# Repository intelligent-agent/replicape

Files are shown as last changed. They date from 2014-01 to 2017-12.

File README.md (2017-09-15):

    :::python
     _____           __
    | ___ \         | (_)
    | |_/ /___ _ __ | |_  ___ __ _ _ __   ___
    |    // _ \  _ \| | |/ __/ _  |  _ \ / _ \
    | |\ \  __/ |_) | | | (_| (_| | |_) |  __/
    \_| \_\___| .__/|_|_|\___\__,_| .__/ \___|
             | |                 | |
             |_|                 |_|

Replicape is a 3D printer cape for BeagleBone.  

### Features: ###

* 5 stepper motors (Trinamic TMC2100) (X, Y, Z, E, H)  
* 3 high power MOSFETs (PWM controlled) for 2 extruders and 1 HPB.  (12..24V)  
* 4 medium power MOSFETs (PWM controlled) for up to 4 fans/LED strips.  (12V)  
* 3 analog input ports for thermistors. noise-filtered inputs and option for shielding  
* 6 inputs for end stops (X, Y, Z).  
* 1 bus for Dallas 1W temperature sensor for monitoring the cold end. Up to 10 sensors can be added to the bus.  
* 2 servo outputs.  
* 1 inductive sensor input.  
* Programmable current limits on steppers motor drivers (SMD). No need to manually adjust a pot meter.  
* Microstepping individually programmable for each SMD from 1 to 256.  
* All steppers are controlled by the Programmable Realtime Unit (PRU) for hard real time operation.  
* Compatible with [Manga Screen](https://bitbucket.org/intelligentagent/manga-screen)  
* Single 12 to 24V PSU, fans are still 12V.  
* Compatible with BeagleBone and BeagleBone Black (probably also green and blue).  
* Open source hardware and software. (CC BY-SA)  
* Software written in Python for maintainability and hackability.  
  
This is the repository for the hardware, the "firmware" (Redeem) has a [separate repository](https://bitbucket.org/intelligentagent/redeem)

### What is in here? ###

* This repository contains the files needed to reproduce the PCB and continue development.
* The latest revision is B3

### I want one! How much is it, and where can I get it? ###

It's $99 and you can [buy it in the store](http://www.thing-printer.com/product/replicape)

### I want to build my own board. How do I do that? ###

* Download the BOM and order the parts from Digi-key
* Send the GERBER files to a PCB manufacturer
* Get a reflow oven
* Populate the board

### I want a different version of this, who do I talk to? ###

Talk to Elias <elias at iagent dot no> 

### I have a Replicape, how do I wire it? ###
Look at the wiki page: [http://wiki.thing-printer.com](http://wiki.thing-printer.com)

### I want to read about the latest development of this board. Where can I do that? ###
The thing-prnter blog is a good place: [http://www.thing-printer.com/blog/](http://www.thing-printer.com/blog/)

### Who has contributed to this project? ###

* Elias Bakken
* Dirk Eichel
* Stoneshop
* Bent Furevik

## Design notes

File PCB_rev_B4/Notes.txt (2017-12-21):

TODO: 
 + Add 41 pin connector, place it near the Ethernet cable. 
 - Keep the connectors that we have, change end stop wiring, so they are not tied to common ground. 
 - 4 x 12V fans!
 - RTD drop in replacement, Add jumper to Select voltage divider for RTD1000
 - Double check the final price.
 - Add a second thermistor for measuring chamber tmeperature, use T1 for that.
 - Perhaps use pin 1 and 2 for T1? 
 - Check price on EuroCircuits for 2 and 15 boards. 

Notes: 
 + Needs to either move the BBB, longer 41 pin cable or add a mounting plate. 
 - Choosing horizontal 41 pin connector to keep profile low. 
 - Pin 9/10 Not connected to anything. Is this right? 
 - Choosing 0.3 mm traces for Stepper X and E, due to 24V input. 
 - Do not use keyed horizontal headers.

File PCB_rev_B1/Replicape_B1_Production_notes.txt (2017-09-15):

Solder mask color: Black
Silkscreen color: White
PCB Layers: 4

Copper thickness: 35um

Top copper layer: Replicape_B1.cmp
Inner copper layer 1: Replicape_B1.ly2
Inner copper layer 2: Replicape_B1.l15
Bottom copper layer: Replicape_B1.sol

Outline: Replicape_B1.pls

Solder stop mask top layer: Replicape_B1.stc
Silk screen top layer: Replicape_B1.plc
Cream frame top: Replicape_B1.crc

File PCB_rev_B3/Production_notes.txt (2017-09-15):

Solder mask color: Black
Silkscreen color: White
PCB Layers: 4

Copper thickness: 35um

Top copper layer: Replicape_B3.cmp
Inner copper layer 1: Replicape_B3.ly2
Inner copper layer 2: Replicape_B3.l15
Bottom copper layer: Replicape_B3.sol

Outline: Replicape_B3.pls

Solder stop mask top layer: Replicape_B3.stc
Silk screen top layer: Replicape_B3.plc
Cream frame top: Replicape_B3.crc

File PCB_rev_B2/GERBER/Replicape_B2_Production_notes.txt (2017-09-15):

Solder mask color: Black
Silkscreen color: White
PCB Layers: 4

Copper thickness: 35um

Top copper layer: Replicape_B2.cmp
Inner copper layer 1: Replicape_B2.ly2
Inner copper layer 2: Replicape_B2.l15
Bottom copper layer: Replicape_B2.sol

Outline: Replicape_B2.pls

Solder stop mask top layer: Replicape_B2.stc
Silk screen top layer: Replicape_B2.plc
Cream frame top: Replicape_B2.crc

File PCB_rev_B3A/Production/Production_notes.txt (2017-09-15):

Solder mask color: Black
Silkscreen color: White
PCB Layers: 4

Copper thickness: 35um

Top copper layer: Replicape_B3A.cmp
Inner copper layer 1: Replicape_B3A.ly2
Inner copper layer 2: Replicape_B3A.l15
Bottom copper layer: Replicape_B3A.sol

Outline: Replicape_B3A.pls

Solder stop mask top layer: Replicape_B3A.stc
Silk screen top layer: Replicape_B3A.plc
Cream frame top: Replicape_B3A.crc

Statistics: 
===========
Length: 107.30 mm
Height: 69.55 mm
Number of SMD pads: 825
Number of Through holes: 167

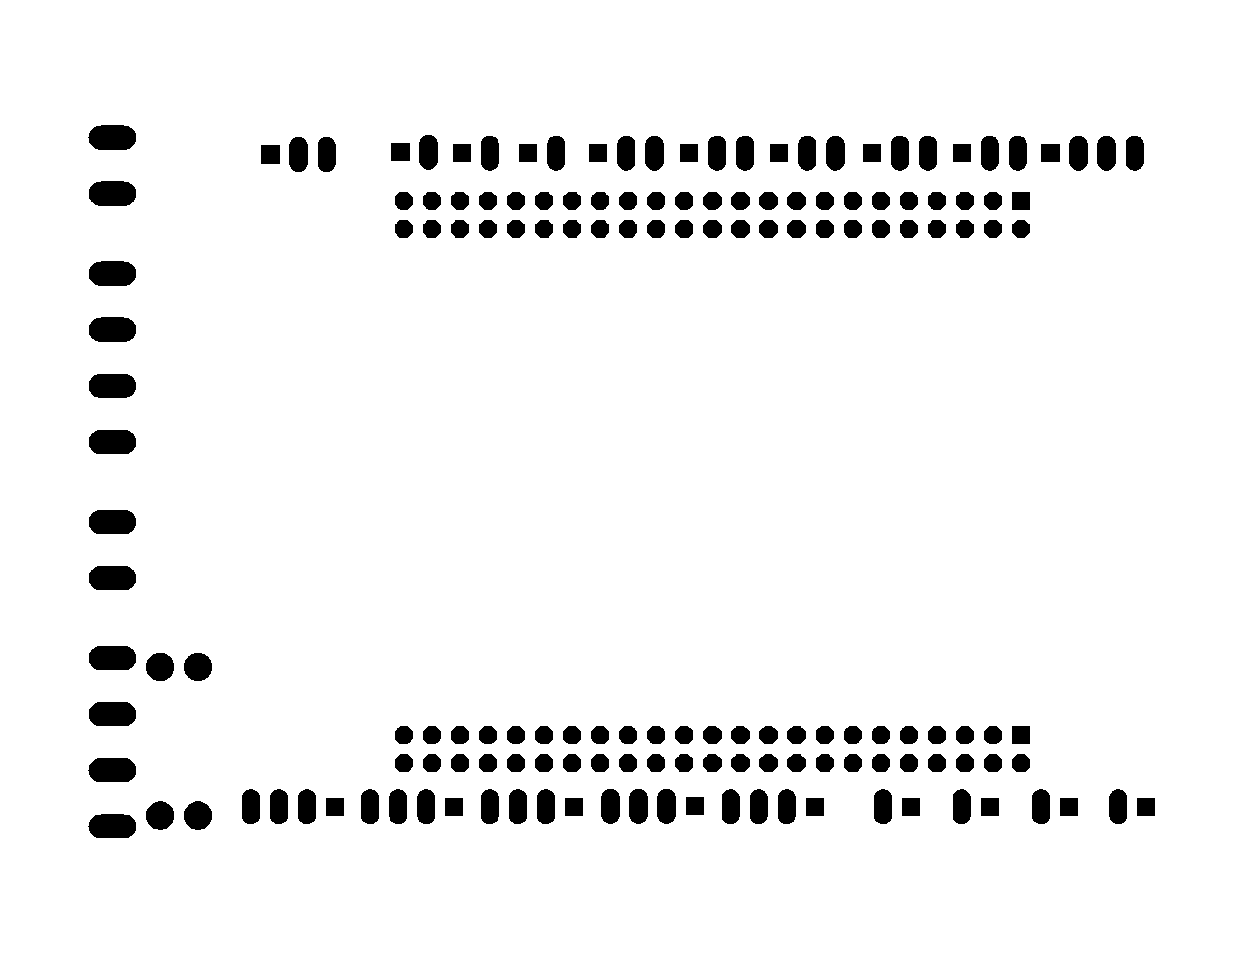
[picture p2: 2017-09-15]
PCB_rev_B2/eagleUp/eagleUp_Replicape_B2_bottom_mask.png

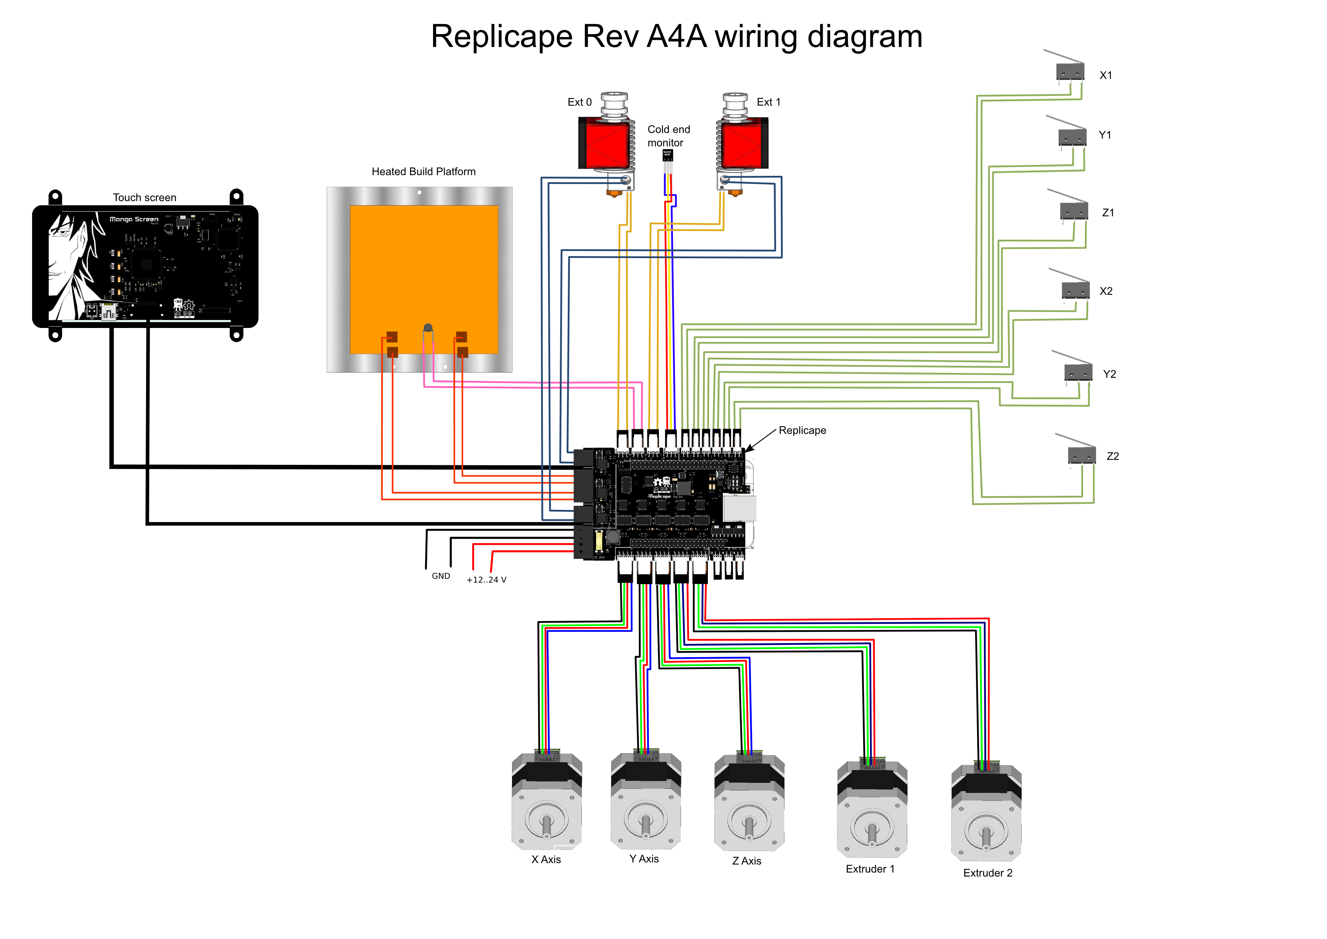
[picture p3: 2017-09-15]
PCB_rev_A4A/Replicape-wire-diagram.png

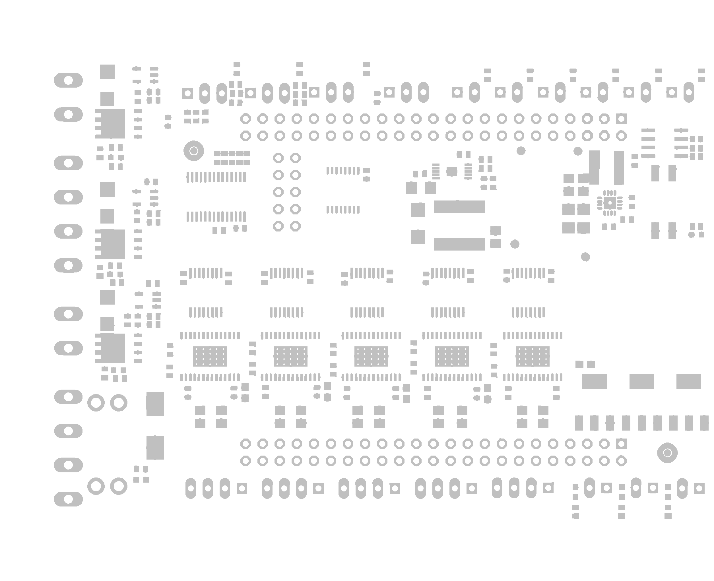
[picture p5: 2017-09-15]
PCB_rev_A4A/eagleUp/pads.png

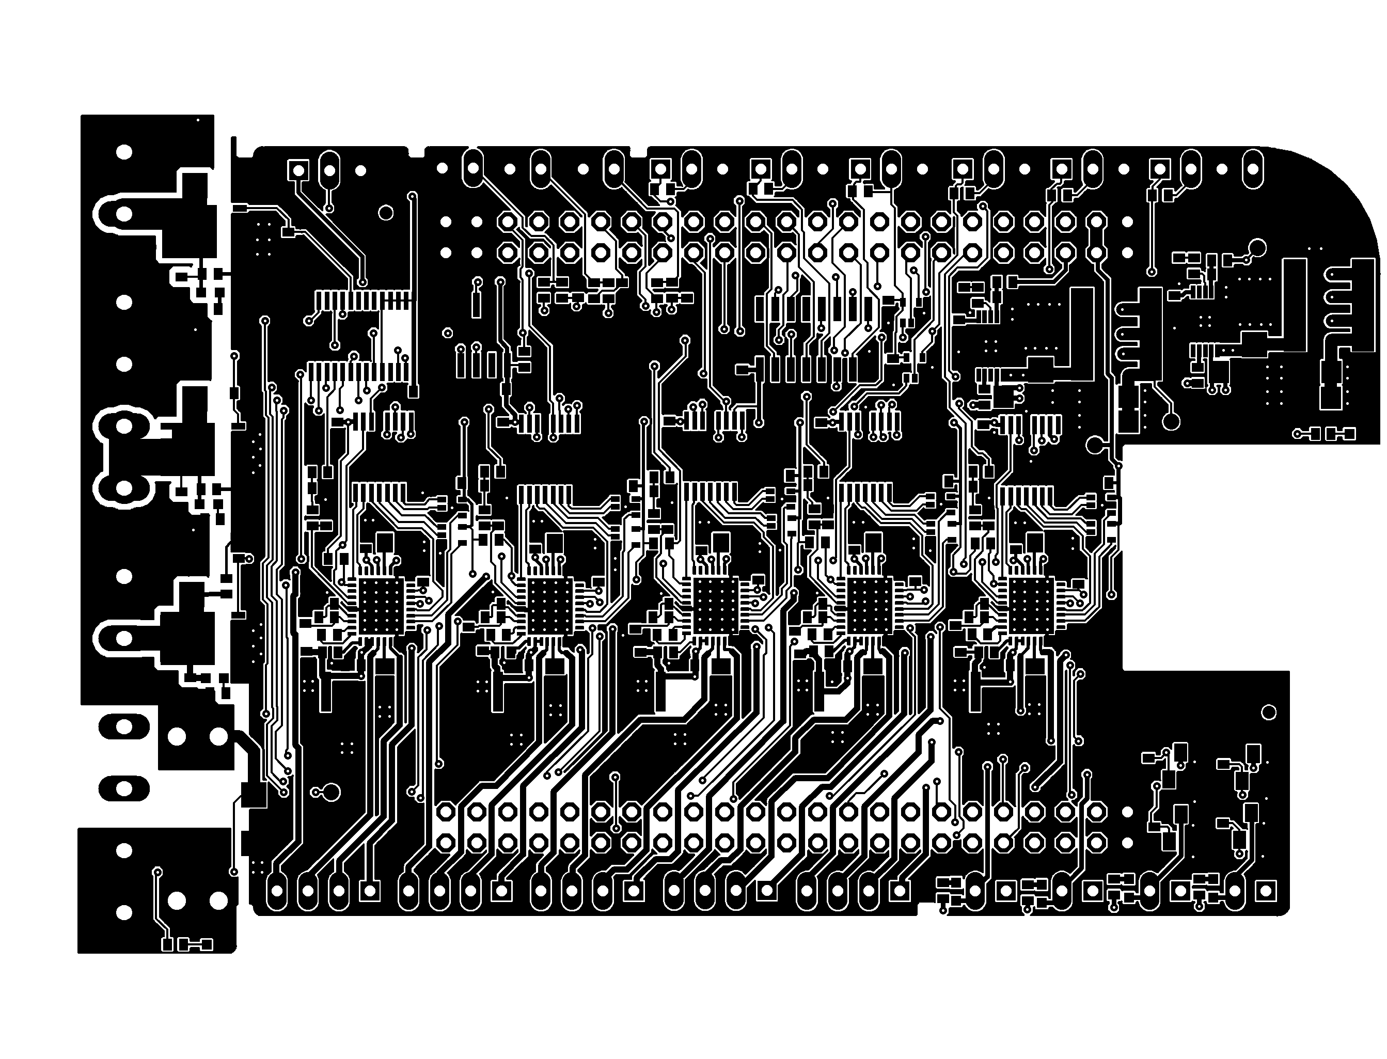
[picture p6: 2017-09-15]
PCB_rev_B2/eagleUp/eagleUp_Replicape_B2_top.png

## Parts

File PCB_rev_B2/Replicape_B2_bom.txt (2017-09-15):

Partlist exported from /home/elias/workspace/replicape/PCB_rev_B2/Replicape_B2.sch at 30.07.15 20:18

Qty Value                  Device                 Package              Parts                                                                                                                                                                                                                      Description                                                                       MF      MPN           OC_FARNELL OC_NEWARK PACKAGE  SUPPLIER          TOLERANCE TP_SIGNAL_NAME VALUE VOLTAGERATING
4                          NPN-TRANSISTOR_SOT23   SOT23                Q4, Q5, Q6, Q7                                                                                                                                                                                                             NPN TRANSISTOR                                                                                                                                                                                      
10  0.1R                   R-EU_R0805             R0805                R1, R2, R3, R4, R7, R8, R9, R10, R29, R30                                                                                                                                                                                  RESISTOR, European symbol                                                                                                                                                                           
45  0.1uF                  C-EUC0402              C0402                C2, C4, C5, C6, C8, C10, C13, C14, C15, C17, C19, C20, C22, C23, C27, C28, C29, C30, C31, C32, C35, C38, C40, C41, C42, C43, C44, C61, C63, C64, C66, C67, C69, C70, C71, C72, C73, C74, C82, C83, C84, C85, C86, C87, C88 CAPACITOR, European symbol                                                                                                                                                                          
5   100UF                  EEE-FK1V101XP-CASE-D8  CAPAE660X800N        C11, C16, C24, C34, C60                                                                                                                                                                                                    Aluminum Electrolytic Capacitors,Surface Mount Type                                       EEE-FK1V101XP 1850114    23T0869   CASE-D8  PANASONIC         ±20 %                    100UF 35V          
15  10K                    R-EU_R0402             R0402                R6, R22, R27, R31, R35, R37, R38, R39, R40, R41, R43, R49, R50, R58, R60                                                                                                                                                   RESISTOR, European symbol                                                                                                                                                                           
4   10nF                   C-EUC0402              C0402                C49, C50, C54, C55                                                                                                                                                                                                         CAPACITOR, European symbol                                                                                                                                                                          
6   10uF                   C-EUC1206              C1206                C47, C48, C52, C53, C80, C81                                                                                                                                                                                               CAPACITOR, European symbol                                                                                                                                                                          
1   120K                   R-EU_R0402             R0402                R42                                                                                                                                                                                                                        RESISTOR, European symbol                                                                                                                                                                           
2   1nF                    C-EUC0402              C0402                C51, C56                                                                                                                                                                                                                   CAPACITOR, European symbol                                                                                                                                                                          
5   2.2R                   R-EU_R0402             R0402                R52, R53, R59, R70, R71                                                                                                                                                                                                    RESISTOR, European symbol                                                                                                                                                                           
7   22-05-7028-02          22-05-7028-02          7395-02              X4, X5, X6, X7, X8, X9, X11                                                                                                                                                                                                CONNECTOR                                                                                               9731601    unknown                                                                          
6   22-05-7038-03          22-05-7038-03          7395-03              X1, X10, X13, X19, X22, X23                                                                                                                                                                                                CONNECTOR                                                                                               unknown    unknown                                                                          
6   22-05-7048-04          22-05-7048-04          7395-04              X12, X14, X15, X16, X17, X18                                                                                                                                                                                               CONNECTOR                                                                                               unknown    unknown                                                                          
5   22nF                   C-EUC0402              C0402                C1, C3, C7, C9, C39                                                                                                                                                                                                        CAPACITOR, European symbol                                                                                                                                                                          
2   33uH                   RT8040T330             NR8040T330           L1, L2                                                                                                                                                                                                                                                                                                                                                                                                                         
2   39K                    R-EU_R0402             R0402                R26, R44                                                                                                                                                                                                                   RESISTOR, European symbol                                                                                                                                                                           
31  4.7K                   R-EU_R0402             R0402                R5, R11, R14, R15, R16, R19, R20, R21, R23, R24, R25, R28, R32, R33, R34, R36, R45, R46, R47, R48, R51, R54, R55, R56, R57, R61, R62, R63, R64, R65, R66                                                                   RESISTOR, European symbol                                                                                                                                                                           
3   4.7nF                  C-EUC0402              C0402                C57, C58, C59                                                                                                                                                                                                              CAPACITOR, European symbol                                                                                                                                                                          
18  4.7uF                  C-EUC0402              C0402                C12, C18, C21, C25, C26, C33, C36, C37, C45, C46, C62, C65, C68, C75, C76, C77, C78, C79                                                                                                                                   CAPACITOR, European symbol                                                                                                                                                                          
1   44.3K                  R-EU_R0402             R0402                R12                                                                                                                                                                                                                        RESISTOR, European symbol                                                                                                                                                                           
3   4K7, 1%                R-EU_R0402             R0402                R13, R17, R18                                                                                                                                                                                                              RESISTOR, European symbol                                                                                                                                                                           
12  74AHC1G126DCK          74AHC1G126DCK          SC70-5               IC3, IC4, IC6, IC7, IC8, IC9, IC10, IC11, IC13, IC14, IC16, IC17                                                                                                                                                           Single Bus Buffer Gate With 3-State Outputs                                                                                                                                                         
3   AON6758                AON6758                8-DFN-EP-(5X6)       Q1, Q2, Q3                                                                                                                                                                                                                                                                                                                                                                                                                     
1   CAT24C256              CAT24C256              SOIC127P600X175-8N   U18                                                                                                                                                                                                                                                                                                                                                                                                                            
1   CC-BY-SA               CC-BY-SA               CC-BY-SA             U$3                                                                                                                                                                                                                                                                                                                                                                                                                            
1   CD4050BD               CD4050BD               SOIC127P600X175-16N  U19                                                                                                                                                                                                                        CMOS Hex Buffer/Converters                                                                CD4050BD      1740857    50R5062   16-SOIC  Texas Instruments                                             
2   F-2X23-                F-2X23-                DIL-100-2X23         P8, P9                                                                                                                                                                                                                                                                                                                                                                                                                         
2   FIDUCIAL1X2.5          FIDUCIAL1X2.5          FIDUCIAL-1X2.5       JP1, JP2                                                                                                                                                                                                                   Fiducial Alignment Points                                                                                                                                                                           
1   FUSE                   FUSE                   3557                 F1                                                                                                                                                                                                                         Fuse                                                                                                                                                                                                
6   MBRA340T3              MBRA340T3              SMA                  D1, D2, D3, D4, D5, D6                                                                                                                                                                                                     Surface Mount Schottky Power Rectifier                                                                                                                                                              
2   MSTBA2                 MSTBA2                 MSTBA2               X3, X21                                                                                                                                                                                                                    PHOENIX                                                                           FARNELL 1757242       3705171    71C4161                                                                          
2   MSTBA4                 MSTBA4                 MSTBA4               X2, X20                                                                                                                                                                                                                    PHOENIX                                                                           FARNELL 1757268       3705195    71C4163                                                                          
1   OSHW_LOGO_FILLX0200-NT OSHW_LOGO_FILLX0200-NT OSHW_FILLX200_NOTEXT LOGO1                                                                                                                                                                                                                                                                                                                                                                                                                          
1   PCA9685PW              PCA9685PW              SOP65P640X110-28N    U11                                                                                                                                                                                                                        16-channel, 12-bit PWM Fm+ I2C-bus LED controller                                         PCA9685PW     1854074    19T6398   TSSOP-28 NXP                                                           
2   RT8268                 RT8268                 MSOP10               U6, U10                                                                                                                                                                                                                                                                                                                                                                                                                        
5   SN74AHC595PW           SN74AHC595PW           SOP65P640X120-16N    U1, U2, U3, U4, U5                                                                                                                                                                                                         8 bit shift registers with 3-state  output registers                                      SN74AHC595PW  1741463    50R5930   TSSOP-16 Texas Instruments                                             
5   TMC2100-LA             TMC2100-LA             QFN36-PAD            IC1, IC2, IC5, IC12, IC15                                                                                                                                                                                                  Trinamic TMC2100 Stepper Motor Driver (5V...46V, 1.2A, peak 1.7A, 256 microsteps)                                                                                                                   
4   TPB1,27                TPB1,27                B1,27                3.3V, 5V, 12..24V, 12V                                                                                                                                                                                                     Test pad                                                                                                                                                                                            
9   blue                   LEDCHIP-LED0603        CHIP-LED0603         LED1, LED2, LED3, LED4, LED5, LED6, LED7, LED8, LED9                                                                                                                                                                       LED

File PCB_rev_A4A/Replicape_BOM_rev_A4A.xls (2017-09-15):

Digikey Part nr. | Desc | Ref | QTY 1 | P. ea 1 | P. ext 1 | QTY 500 | P. ea 500 | P. ext 500
Connectors
A19450-ND | CONN HEADER RTANG 2POS .100 TIN | X1, X4, X5, X6, X10, X11, X13, X19, X23 | 9 | 0.1 | 0.9 | 4500 | 0.03768 | 169.56
A19451-ND | CONN HEADER RTANG 3POS .100 TIN | X7, X8, X9, X12 | 4 | 0.14 | 0.56 | 2000 | 0.05733 | 114.66
A19452-ND | CONN HEADER RTANG 4POS .100 TIN | X14, X15, X16, X17, X18 | 5 | 0.18 | 0.9 | 2500 | 0.08734 | 218.35
WM7847-ND | CONN HEADER 4POS 5.08MM R/A TIN | X3, X21 | 2 | 1.04 | 2.08 | 1000 | 0.648 | 648
WM7953-ND | CONN TERM BLOCK 4POS 5.08MM R/A | X3-2, X21-2 | 2 | 2.5 | 5 | 1000 | 1.5 | 1500
WM7845-ND | CONN HEADER 2POS 5.08MM R/A TIN | X2, X20 | 2 | 0.64 | 1.28 | 1000 | 0.4 | 400
WM7819-ND | CONN TERM BLOCK 2POS 5.08MM | X2-2, X20-2 | 2 | 1.43 | 2.86 | 1000 | 0.88794 | 887.94
SAM1204-23-ND | CONN RCPT .100" 46POS DUAL TIN | P9-EXPANSION_A, P8-EXPANSION_A | 2 | 4.72 | 9.44 | 1000 | 2.7492 | 2749.2
ICs
296-28915-5-ND | IC CTRLR STEPPER MOTOR 28HTSSOP | U13, U14, U15, U16, U17 | 5 | 6.53 | 32.65 | 2500 | 3.2625 | 8156.25
DAC088S085CIMT/NOPB-ND | IC DAC 8BIT OCTAL R-R 16-TSSOP | U12 | 1 | 3.78 | 3.78 | 500 | 1.755 | 877.5
568-8366-5-ND | IC LED DRIVER RGBA 28-TSSOP | U11 | 1 | 2.36 | 2.36 | 500 | 1.33 | 665
CAT24C256WI-GT3OSCT-ND | IC EEPROM 256KBIT 400KHZ 8SOIC | U18 | 1 | 0.71 | 0.71 | 500 | 0.35536 | 177.68
MCP1402T-E/OTCT-ND | IC MOSFET DRIVER 500MA SOT23-5 | U7, U8, U9 | 3 | 0.74 | 2.22 | 1500 | 0.47 | 705
296-4620-1-ND | IC 8BIT SHFT REG TRI-ST 16-TSSOP | U1, U2, U3, U4, U5 | 5 | 0.49 | 2.45 | 2500 | 0.1326 | 331.5
MCP16321T-500E/NGTR-ND | IC REG BUCK SYNC 5V 1A 16-VQFN | U6 | 1 | 1.86 | 1.86 | 500 |  | 0
1028-1045-1-ND | IC REG BUCK ADJ 2A 10MSOP | U10 | 1 | 0.76 | 0.76 | 500 | 0.38192 | 190.96
Resistors
RL12S.10FCT-ND | RES .10 OHM 1/3W 1% 0805 SMD | R1, R2, R3, R4, R5, R6, R7, R8, R9, R10 | 10 | 0.32 | 3.2 | 5000 | 0.06306 | 315.3
P100JCT-ND | RES 100 OHM 1/10W 5% 0402 SMD | R31, R32, R37, R58 | 4 | 0.1 | 0.4 | 2000 | 0.0072 | 14.4
311-4.7KJRCT-ND | RES 4.7K OHM 1/16W 5% 0402 SMD | R11, R12, R14, R15, R16, R19, R20, R21, R22, R23, R24, R25, R26, R27, R28, R29, R30, R33, R34, R35, R36, R45, R46, R47, R48, R55, R56, R57 | 28 | 0.012 | 0.336 | 14000 | 0.00336 | 47.04
P4.70KLCT-ND | RES 4.7K OHM 1/10W 1% 0402 SMD | R13, R17, R18 | 3 | 0.1 | 0.3 | 1500 | 0.01008 | 15.12
P6.8KJCT-ND | RES 6.8K OHM 1/10W 5% 0402 SMD | R38, R39, R40 | 3 | 0.1 | 0.3 | 1500 | 0.0072 | 10.8
P10KJCT-ND | RES 10K OHM 1/10W 5% 0402 SMD | R41, R43 | 2 | 0.1 | 0.2 | 1000 | 0.0072 | 7.2
RMCF0402FT40K2CT-ND | RES 40.2K OHM 1/16W 1% 0402 | R44 | 1 | 0.04 | 0.04 | 500 | 0.00576 | 2.88
RMCF0402FT120KCT-ND | RES 120K OHM 1/16W 1% 0402 | R42 | 1 | 0.04 | 0.04 | 500 | 0.00576 | 2.88
MOSFETs
AUIPS1051L-ND | IC SW IPS 1CH LOW SIDE SOT223 | Q4, Q5, Q6 | 3 | 1.28 | 3.84 | 1500 | 0.51294 | 769.41
785-1370-1-ND | MOSFET N-CH 30V 32A 8DFN | Q1, Q2, Q3 | 3 | 0.8 | 2.4 | 1500 | 0.4004 | 600.6
Capacitors
445-1256-1-ND | CAP CER 1000PF 50V 10% X7R 0402 | C56 | 1 | 0.1 | 0.1 | 500 | 0.0077 | 3.85
445-1261-1-ND | CAP CER 0.022UF 25V 10% X7R 0402 | C51 | 1 | 0.1 | 0.1 | 500 | 0.0104 | 5.2
587-2237-1-ND | CAP CER 4700PF 50V 10% X7R 0402 | C57, C58, C59 | 3 | 0.08 | 0.24 | 1500 | 0.0096 | 14.4
311-1360-1-ND | CAP CER 10000PF 25V 10% X7R 0603 | C1, C3, C5, C7, C9, C54, C55 | 7 | 0.1 | 0.7 | 3500 | 0.00648 | 22.68
445-4964-1-ND | CAP CER 0.1UF 25V 10% X5R 0402 | C2, C4, C6, C8, C10, C11, C13, C17, C19, C20, C22, C24, C27, C29, C31, C33, C35, C36, C37, C38, C39, C40, C41, C42, C43, C44 | 26 | 0.04 | 1.04 | 13000 | 0.0102 | 132.6
445-4996-1-ND | CAP CER 0.47UF 6.3V 10% X5R 0402 | C14, C15, C16, C26, C45, C46 | 6 | 0.1 | 0.6 | 3000 | 0.0231 | 69.3
1276-1903-1-ND | CAP CER 4.7UF 25V 20% X5R 0603 | C18, C21, C23, C25, C28, C30, C32, C34 | 8 | 0.3 | 2.4 | 4000 | 0.08188 | 327.52
445-11700-1-ND | CAP CER 10UF 25V 20% JB 1206 | C47, C48, C52 | 3 | 0.56 | 1.68 | 1500 | 0.196 | 294
1276-2412-1-ND | CAP CER 22UF 6.3V 20% X5R 0805 | C49, C50, C53 | 3 | 0.27 | 0.81 | 1500 | 0.066 | 99
PCE3917CT-ND | CAP ALUM 100UF 50V 20% SMD | C12 | 1 | 0.81 | 0.81 | 500 | 0.33496 | 167.48
Diodes/LEDs
475-2816-1-ND | LED CHIPLED BLUE 470NM 0603 SMD | LED1, LED2, LED3, LED4, LED5, LED6, LED7 | 7 | 0.21 | 1.47 | 3500 | 0.11178 | 391.23
475-3016-1-ND | LED POINTLED 628NM SUPER RED SMD | LED8 | 1 | 0.08 | 0.08
MBRA340T3GOSCT-ND | DIODE SCHOTTKY 40V 3A SMA | D1, D2, D3, D4 | 4 | 0.53 | 2.12 | 2000 | 0.24812 | 496.24
Inductors
445-6517-1-ND | INDUCTOR POWER 4.7UH 2.0A SMD | L1 | 1 | 0.45 | 0.45 | 500 | 0.26 | 130
587-2636-1-ND | INDUCTOR 33UH 1.7A 20% SMD | L2 | 1 | 0.57 | 0.57 | 500 | 0.37126 | 185.63
Other
F4991-ND | FUSE BLADE LP MINI 58V SILVR 20 | F1 | 1 | 0.96 | 0.96 | 500 | 0.495 | 247.5
3557K-ND | FUSE CLIP UNIVERSL AUTO BLADE PC | F1-1 | 2 | 0.21 | 0.42 | 1000 | 0.1148 | 114.8
CT2192MST-ND | SWITCH TAPE SEAL 2 POS SMD | S1 | 1 | 0.6 | 0.6 | 500 | 0.43302 | 216.51
Sum |  |  |  |  | 96.016 |  |  | 44.99034

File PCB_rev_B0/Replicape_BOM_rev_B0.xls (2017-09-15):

Digikey Part nr. | Mnf. Part Nr | Manuf. | Package | Desc | Ref | QTY 1 | P. ea 1 | P. ext 1 | QTY 500 | P. ea 500 | P. ext 500
Connectors
A19450-ND | 640455-2 | TE |  | CONN HEADER RTANG 2POS .100 TIN | X1, X4, X5, X6, X10, X11, X13, X19, X23 | 7 | 0.1 | 0.7 | 3500 | 0.037 | 129.50 | 0.037
A19451-ND | 640455-3 | TE |  | CONN HEADER RTANG 3POS .100 TIN | X7, X8, X9, X12 | 6 | 0.14 | 0.84 | 3000 | 0.052 | 156.00 | 0.052
A19452-ND | 640455-4 | TE |  | CONN HEADER RTANG 4POS .100 TIN | X14, X15, X16, X17, X18 | 5 | 0.18 | 0.9 | 2500 | 0.08734 | 218.35 | 0.069
WM7847-ND | 395321004 | Molex |  | CONN HEADER 4POS 5.08MM R/A TIN | X3, X21 | 2 | 1.04 | 2.08 | 1000 | 0.648 | 648.00
WM7953-ND | 395300004 | Molex |  | CONN TERM BLOCK 4POS 5.08MM R/A | X3-2, X21-2 | 2 | 2.5 | 5 | 1000 | 1.5 | 1500.00
WM7845-ND | 395321002 | Molex |  | CONN HEADER 2POS 5.08MM R/A TIN | X2, X20 | 2 | 0.64 | 1.28 | 1000 | 0.4 | 400.00 | 0.264
WM7819-ND | 395300002 | Molex |  | CONN TERM BLOCK 2POS 5.08MM | X2-2, X20-2 | 2 | 1.43 | 2.86 | 1000 | 0.88794 | 887.94 | 0.688
SAM1204-23-ND |  | Samtec |  | CONN RCPT .100" 46POS DUAL TIN | P9-EXPANSION_A, P8-EXPANSION_A | 2 | 4.95 | 9.9 | 1000 | 2.47463
 | SSHQ-123-D-08-F-LF | MAJOR LEAGUE |  | CONN RCPT .100" 46POS DUAL TIN | P9-EXPANSION_A, P8-EXPANSION_A | 2 |  |  | 1000 | 1.47 | 1470.00 | 2.7
ICs |  |  |  |  |  |  |  |  |  |  |  | 1.33
296-28915-5-ND | DRV8825PWPR | TI |  | IC CTRLR STEPPER MOTOR 28HTSSOP | U13, U14, U15, U16, U17 | 5 | 6.53 | 32.65 | 2500 | 2.7 | 6750.00 | 0.92
568-8366-5-ND | PCA9685PW,112 | NXP |  | IC LED DRIVER RGBA 28-TSSOP | U11 | 1 | 2.36 | 2.36 | 500 | 1.33 | 665.00 | 0.12342
MCP16321T-500E/NGTR-ND | MCP16321T-500E/NG | Microchip |  | IC REG BUCK SYNC 5V 1A 16-VQFN | U6 | 1 | 1.86 | 1.86 | 500 | 0.92 | 460.00 | 0.33936
MC74HC595ADTR2GOSTR-ND | MC74HC595ADTR2G | ON |  | IC SHIFT REGSTR 8BIT 3ST 16TSSOP | U1, U2, U3, U4, U5 | 5 | 0.5 | 2.5 | 2500 | 0.12342 | 308.55 | 0.103
CAT24C256WI-GT3OSCT-ND | CAT24C256WI-GT3 | ON |  | IC EEPROM 256KBIT 400KHZ 8SOIC | U18 | 1 | 0.71 | 0.71 | 500 | 0.33936 | 169.68 | 0.38564
ZXGD3009DYTADICT-ND | ZXGD3009DYTA | Diodes Inc | SOT363 | IC GATE DRVR IGBT/MOSFET SOT363 | U7, U8, U9 | 3 | 0.49 | 1.47 | 1500 | 0.134 | 201.00 | 0.05819
1028-1045-1-ND | RT8268GFP | Richtek |  | IC REG BUCK ADJ 2A 10MSOP | U10 | 1 | 0.76 | 0.76 | 500 | 0.38192 | 190.96 | 0.177
M74VHC1GT126DF1GOSTR-ND | M74VHC1GT126DF1G | ON |  | M74VHC1GT126DF1G | 5xMixedMode, 2xServoOut | 2 | 0.36 | 2.52 | 3500 | 0.05819 | 203.66 | 0.03308
296-31503-2-ND | CD4050BPWR | TI |  | CD4050, 18V tolerant buffer | 1x | 1 | 0.45 | 0.45 | 500 | 0.21112 | 105.56 | 0.00384
 |  |  |  |  |  |  |  |  |  |  |  | 0.00134
Resistors |  |  |  |  |  |  |  |  |  |  |  | 0.00544
RL12S.10FCT-ND |  |  |  | RES .10 OHM 1/3W 1% 0805 SMD | R1, R2, R3, R4, R5, R6, R7, R8, R9, R10 | 10 | 0.32 | 3.2 | 5000 | 0.06306 | 315.30 | 0.0027
P100JCT-ND |  |  |  | RES 100 OHM 1/10W 5% 0402 SMD | R31, R32, R37, R58 | 4 | 0.1 | 0.4 | 2000 | 0.0072 | 14.40 | 0.00576
311-4.7KJRCT-ND |  |  |  | RES 4.7K OHM 1/16W 5% 0402 SMD | R11, R12, R14, R15, R16, R19, R20, R21, R22, R23, R24, R25, R26, R27, R28, R29, R30, R33, R34, R35, R36, R45, R46, R47, R48, R55, R56, R57 | 38 | 0.012 | 0.456 | 19000 | 0.00336 | 63.84 | 0.00576
P4.70KLCT-ND |  |  |  | RES 4.7K OHM 1/10W 1% 0402 SMD | R13, R17, R18 | 3 | 0.1 | 0.3 | 1500 | 0.01008 | 15.12 | 0.403
P10KJCT-ND |  |  |  | RES 10K OHM 1/10W 5% 0402 SMD |  | 10 | 0.1 | 1 | 5000 | 0.0072 | 36.00 | 0.3003
RMCF0402FT40K2CT-ND |  |  |  | RES 40.2K OHM 1/16W 1% 0402 | R44 | 1 | 0.04 | 0.04 | 500 | 0.00576 | 2.88 | 0.0077
RMCF0402FT120KCT-ND |  |  |  | RES 120K OHM 1/16W 1% 0402 | R42 | 1 | 0.04 | 0.04 | 500 | 0.00576 | 2.88 | 0.0106
RHM1.00MCDCT-ND | MCR01MRTF1004 | Rohm | 402 | RES SMD 1M OHM 1% 1/16W 0402 |  | 5 | 0.1 |  | 2500 | 0.00233 | 5.83
MOSFETs | MCR01MRTF1004 |  |  |  |  |  |  |  |  |  |  | 0.00543
ZXMS6004FFCT-ND |  | Diodes Inc |  | MOSFET N-CH 60V 1.3A SOT23F | Q4, Q5, Q6 | 4 | 0.94 | 3.76 | 2000 | 0.403 | 611.00 | 0.00441
785-1370-1-ND | AON6758 |  |  | MOSFET N-CH 30V 32A 8DFN | Q1, Q2, Q3 | 3 | 0.8 | 2.4 | 1500 | 0.4004 | 600.60 | 0.018
Capacitors |  |  |  |  |  |  |  |  |  |  |  | 0.03118
445-1256-1-ND |  |  | 402 | CAP CER 1000PF 50V 10% X7R 0402 | C56 | 1 | 0.1 | 0.1 | 500 | 0.0077 | 3.85 | 0.18
445-1261-1-ND |  |  | 402 | CAP CER 0.022UF 25V 10% X7R 0402 | C51 | 1 | 0.1 | 0.1 | 500 | 0.0104 | 5.20 | 0.0561
311-1360-1-ND |  |  | 402 | CAP CER 10000PF 25V 10% X7R 0603 | C1, C3, C5, C7, C9, C54, C55 | 7 | 0.1 | 0.7 | 3500 | 0.00648 | 22.68 | 0.13906
490-10459-1-ND |  | Murata | 603 | CAP CER 0.1UF 100V 20% X5R 0402 | C2, C4, C6, C8, C10, C11, C13, C17, C19, C20, C22, C24, C27, C29, C31, C33, C35, C36, C37, C38, C39, C40, C41, C42, C43, C44 | 26 | 0.018 | 0.468 | 13000 | 0.00525 | 75.25 | 0.07674
445-4996-1-ND |  |  | 402 | CAP CER 0.47UF 6.3V 10% X5R 0402 | C14, C15, C16, C26, C45, C46 | 6 | 0.1 | 0.6 | 3000 | 0.0231 | 69.30 | 0.17488
490-6453-2-ND | GRM219R61C475KE15D | Murata | 805 | CAP CER 4.7UF 16V 10% X5R 0805 | C12, C16, C21, C23, C25, C26, C30, C32, C45, C46 | 10 | 0.21 | 2.1 | 5000 | 0.03118 | 155.90 | 0.26
445-11700-1-ND |  |  | 1206 | CAP CER 10UF 25V 20% JB 1206 | C47, C48, C52 | 3 | 0.56 | 1.68 | 1500 | 0.196 | 294.00 | 0.351
1276-2412-1-ND |  |  | 805 | CAP CER 22UF 6.3V 20% X5R 0805 | C49, C50, C53 | 3 | 0.27 | 0.81 | 1500 | 0.066 | 99.00 | 0.495
493-6420-2-ND | UCD1V101MCL6GS | Nichicon |  | CAP ALUM 100UF 35V 20% SMD | C12 | 5 | 0.57 | 2.85 | 2500 | 0.147 | 367.50 | 0.09189
Diodes/LEDs
475-2816-1-ND | LTST-C191TBKT | Lite-on | 603 | LED 468NM BLUE CLEAR 0603 SMD | LED1..8 | 9 | 0.46 | 4.14 | 4500 | 0.07524 | 338.58
MBRA340T3GOSCT-ND |  |  |  | DIODE SCHOTTKY 40V 3A SMA | D1, D2, D3, D4, D5 | 5 | 0.53 | 2.65 | 2500 | 0.24812 | 620.30
Inductors
445-6517-1-ND |  |  |  | INDUCTOR POWER 4.7UH 2.0A SMD | L1 | 1 | 0.45 | 0.45 | 500 | 0.26 | 130.00
587-2636-1-ND |  |  |  | INDUCTOR 33UH 1.7A 20% SMD | L2 | 1 | 0.57 | 0.57 | 500 | 0.37126 | 185.63
Other
F4991-ND |  |  |  | FUSE BLADE LP MINI 58V SILVR 20 | F1 | 1 | 0.96 | 0.96 | 500 | 0.495 | 247.50
3557K-ND |  |  |  | FUSE CLIP UNIVERSL AUTO BLADE PC | F1-1 | 2 | 0.21 | 0.42 | 1000 | 0.1148 | 114.80
Sum |  |  |  |  |  |  |  | 99.034 |  |  | 37.72308
 |  |  |  | PCB |  |  |  |  | 500 | 4.088 | 2044
 |  |  |  | Assembly |  |  |  |  | 500 | 2.5 | 1250
 |  |  |  | Package |  |  |  |  | 500 | 1 | 500
 |  |  |  | Testing |  |  |  |  | 500 | 1 | 500
 |  |  |  | MOQ |  |  |  |  |  |  | 200
 |  |  |  | Shipping |  |  |  |  |  |  | 50
Sum manufacturing |  |  |  |  |  |  |  |  |  |  | 9.088
Sum total |  |  |  |  |  |  |  |  |  |  | 46.81108
 |  |  |  | MSRP |  |  |  |  |  |  | 99
 |  |  |  | Earnings |  |  |  |  | 1000 | 52.18892 | 52188.92

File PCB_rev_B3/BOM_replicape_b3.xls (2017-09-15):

Qty | Line Item | Manufacturer | MPN | Octopart URL | Schematic Reference | Internal Part Number | Description | Total Qty (@ Batch Size: 500) | SKU | SKU | SKU | Packaging | Packaging | Packaging | Unit Price (@ Batch Size: 500) | Unit Price (@ Batch Size: 500) | Unit Price (@ Batch Size: 500) | In Stock | In Stock | In Stock | MOQ | MOQ | MOQ | URL | URL | URL | Distributor [Lowest Price (Overall)] | SKU [Lowest Price (Overall)] | Packaging [Lowest Price (Overall)] | Unit Price (@ Batch Size: 500) [Lowest Price (Overall)] | Line Total [Lowest Price (Overall)] | Batch Total [Lowest Price (Overall)] | In Stock [Lowest Price (Overall)] | MOQ [Lowest Price (Overall)] | URL [Lowest Price (Overall)] | Notes
 |  |  |  |  |  |  |  |  | Digi-Key | Mouser | Newark | Digi-Key | Mouser | Newark | Digi-Key | Mouser | Newark | Digi-Key | Mouser | Newark | Digi-Key | Mouser | Newark | Digi-Key | Mouser | Newark
7 | 640455-2 | TE Connectivity | 640455-2 | https://octopart.com/640455-2-te+connectivity-39549640 | X4, X5, X6, X7, X8, X9, X11 |  | CONN HEADER RTANG 2POS .100 TIN | 3500 | A19450-ND | 640455-2 | 98F1853 | Bulk |  |  | 0.037 | 0.037 | 0.041 | 5324 | 6428 | 5179 | 1 | 1 | 1 | https://octopart-clicks.com/click/track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 | /click/track?url=http%3A%2F%2Fwww.mouser.com%2FSearch%2FProductDetail.aspx%3Fqs%3D%252f35zJ5USjokC45OrnUjiew%253d%253d%26utm_source%3Dmousersearchapi%26utm_medium%3Dapi-aggregator%26utm_campaign%3D640455-2%26utm_term%3D640455-2%26utm_content%3DTE+Connectivity&ppid=39549640&sig=000274c&sid=2401&ct=offers | https://octopart-clicks.com/click/track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 | Onlinecomponents.com | 6404552 | Bulk | 0.0264 | 0.1848 | 92.4 | 22658 | 1 | https://octopart-clicks.com/click/track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
6 | 640455-3 | TE Connectivity / AMP | 640455-3 | https://octopart.com/640455-3-te+connectivity+%2F+amp-252830 | X1, X10, X13, X19, X22, X23 |  | CONN HEADER RTANG 3POS .100 TIN | 3000 | A19451-ND | 640455-3 | 34B937 | Bulk |  |  | 0.052 | 0.068 | 0.057 | 3042 | 4725 | 5000 | 1 |  | 1 | /click/track?url=http%3A%2F%2Fwww.digikey.com%2Fproduct-detail%2Fen%2F640455-3%2FA19451-ND%2F258998&ppid=252830&sig=09c5093&sid=459&ct=offers | https://octopart-clicks.com/click/track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 | /click/track?url=http%3A%2F%2Fwww.newark.com%2F34B937&ppid=252830&sig=0364b22&sid=2402&ct=offers | Onlinecomponents.com | 6404553 | Bulk | 0.0379 | 0.2274 | 113.7 | 12626 | 1 | https://octopart-clicks.com/click/track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
6 | 640455-4 | TE Connectivity | 640455-4 | https://octopart.com/640455-4-te+connectivity-39508985 | X12, X14, X15, X16, X17, X18 |  | CONN HEADER RTANG 4POS .100 TIN | 3000 | A19452-ND | 640455-4 | 51F3876 | Bulk |  |  | 0.069 | 0.069 | 0.069 | 10911 | 6814 | 3853 | 1 | 1 | 1 | https://octopart-clicks.com/click/track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 | /click/track?url=http%3A%2F%2Fwww.mouser.com%2FSearch%2FProductDetail.aspx%3Fqs%3D%252f35zJ5USjolIN5b4JrZGlg%253d%253d%26utm_source%3Dmousersearchapi%26utm_medium%3Dapi-aggregator%26utm_campaign%3D640455-4%26utm_term%3D640455-4%26utm_content%3DTE+Connectivity&ppid=39508985&sig=0afb856&sid=2401&ct=offers | https://octopart-clicks.com/click/track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 | Onlinecomponents.com | 6404554 | Bulk | 0.0485 | 0.291 | 145.5 | 22117 | 1 | https://octopart-clicks.com/click/track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
2 | 39532-1004 | Molex | 39532-1004 | https://octopart.com/39532-1004-molex-46662656 | X2, X20 |  | CONN HEADER 4POS 5.08MM R/A TIN | 1000 |  | 39532-1004 | 03N6594 |  |  |  |  | 0.576 | 1.1 |  | 927 | 902 |  | 1 | 1 |  | /click/track?url=http%3A%2F%2Fwww.mouser.com%2FSearch%2FProductDetail.aspx%3Fqs%3DcJvWYcaovXx4bHuMvwQahA%253d%253d%26utm_source%3Dmousersearchapi%26utm_medium%3Dapi-aggregator%26utm_campaign%3D39532-1004%26utm_term%3D39532-1004%26utm_content%3DMolex&ppid=46662656&sig=0e26d8a&sid=2401&ct=offers | /click/track?url=http%3A%2F%2Fwww.newark.com%2F03N6594&ppid=46662656&sig=07b0677&sid=2402&ct=offers | Electro Sonic | 395321004 |  | 0.43 | 0.86 | 430 | 1203 | 1 | https://octopart-clicks.com/click/track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
2 | 39530-0004 | Molex | 39530-0004 | https://octopart.com/39530-0004-molex-4056433 | X2-1, X20-1 |  | CONN TERM BLOCK 4POS 5.08MM R/A | 1000 |  | 39530-0004 | 20M7303 |  |  |  |  | 1.22 | 1.22 |  | 1686 | 234 |  | 1 | 1 |  | /click/track?url=http%3A%2F%2Fwww.mouser.com%2FSearch%2FProductDetail.aspx%3Fqs%3DcJvWYcaovXzY3zXnMJaAzw%253d%253d%26utm_source%3Dmousersearchapi%26utm_medium%3Dapi-aggregator%26utm_campaign%3D39530-0004%26utm_term%3D39530-0004%26utm_content%3DMolex&ppid=4056433&sig=026eb16&sid=2401&ct=offers | /click/track?url=http%3A%2F%2Fwww.newark.com%2F20M7303&ppid=4056433&sig=06338f2&sid=2402&ct=offers | Heilind Electronics | MOL39530-0004 | Bulk | 0.8873 | 1.7746 | 887.3 | 847 | 0 | https://octopart-clicks.com/click/track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
2 | 39532-1002 | Molex | 39532-1002 | https://octopart.com/39532-1002-molex-655395 | X3, X21 |  | CONN HEADER 2POS 5.08MM R/A TIN | 1000 |  | 39532-1002 | 20M7342 |  |  |  |  | 0.264 | 0.264 |  | 573 | 1040 |  | 1 | 1 |  | /click/track?url=http%3A%2F%2Fwww.mouser.com%2FSearch%2FProductDetail.aspx%3Fqs%3DcJvWYcaovXwFNJ6GPFZT%25252bQ%253d%253d%26utm_source%3Dmousersearchapi%26utm_medium%3Dapi-aggregator%26utm_campaign%3D39532-1002%26utm_term%3D39532-1002%26utm_content%3DMolex&ppid=655395&sig=01555ae&sid=2401&ct=offers | /click/track?url=http%3A%2F%2Fwww.newark.com%2F20M7342&ppid=655395&sig=0a886cf&sid=2402&ct=offers | Electro Sonic | 395321002 |  | 0.213 | 0.426 | 213 | 248 | 1 | https://octopart-clicks.com/click/track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
2 | 039530-0002 | Molex | 039530-0002 | https://octopart.com/039530-0002-molex-11928398 | X3-1, X21-1 |  | CONN TERM BLOCK 2POS 5.08MM | 1000 | WM7819-ND | 039530-0002 | 20M7301 | Bag |  |  | 0.688 | 0.923 | 0.688 | 4986 | 21285 | 1235 | 1 |  | 1 | https://octopart-clicks.com/click/track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 | https://octopart-clicks.com/click/track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 | https://octopart-clicks.com/click/track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 | Verical | 395300002 |  | 0.4585 | 0.917 | 458.5 | 1942 | 1 | https://octopart-clicks.com/click/track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
2 | SSHQ-123-D-08-F-LF | Major League Electronics | SSHQ-123-D-08-F-LF | https://octopart.com/sshq-123-d-08-f-lf-major+league+electronics-46688507 | P8, P9 |  | CONN RCPT .100" 46POS DUAL TIN""" | 1000 |  |  |  |  |  |  |  |  |  |  |  |  |  |  |  |  |  |  | Future Electronics | SSHQ-123-D-08-F-LF |  | 1.7333 | 3.4666 | 1733.3 | 76 | 10 | https://octopart-clicks.com/click/track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
5 | TMC2100-LA-T | Trinamic | TMC2100-LA-T | https://octopart.com/tmc2100-la-t-trinamic-55645385 | IC1, IC2, IC5, IC12, IC15 |  | IC STEPPER MOTOR DRIVER 32QFN | 2500 | 1460-1128-2-ND |  |  | Tape & Reel |  |  | 2.50692 |  |  | 2000 |  |  | 2000 |  |  | /click/track?url=http%3A%2F%2Fwww.digikey.com%2Fproduct-detail%2Fen%2FTMC2100-LA-T%2F1460-1128-2-ND%2F5144062&ppid=55645385&sig=05520c1&sid=459&ct=offers |  |  | Digi-Key | 1460-1128-2-ND | Tape & Reel | 2.50692 | 12.5346 | 6267.3 | 2000 | 2000 | /click/track?url=http%3A%2F%2Fwww.digikey.com%2Fproduct-detail%2Fen%2FTMC2100-LA-T%2F1460-1128-2-ND%2F5144062&ppid=55645385&sig=05520c1&sid=459&ct=offers
1 | PCA9685PW,112 | NXP Semiconductors | PCA9685PW,112 | https://octopart.com/pca9685pw%2C112-nxp+semiconductors-11764380 | U11 |  | IC LED DRIVER RGBA 28-TSSOP | 500 | 568-8366-5-ND | PCA9685PW,112 | 70R6800 | Tube |  |  | 1.33 | 1.33 | 1.17 | 1463 | 1208 | 631 | 1 | 1 | 1 | /click/track?url=http%3A%2F%2Fwww.digikey.com%2Fproduct-detail%2Fen%2FPCA9685PW%252c112%2F568-8366-5-ND%2F2034324&ppid=11764380&sig=05f654e&sid=459&ct=offers | /click/track?url=http%3A%2F%2Fwww.mouser.com%2FSearch%2FProductDetail.aspx%3Fqs%3D6YAT8rHPFU9wZqiAeiOMZw%253d%253d%26utm_source%3Dmousersearchapi%26utm_medium%3Dapi-aggregator%26utm_campaign%3DPCA9685PW%2C112%26utm_term%3DPCA9685PW%2C112%26utm_content%3DNXP+Semiconductors&ppid=11764380&sig=0b69d7b&sid=2401&ct=offers | /click/track?url=http%3A%2F%2Fwww.newark.com%2F70R6800&ppid=11764380&sig=033b3f9&sid=2402&ct=offers | Future Electronics | PCA9685PW,112 |  | 1.0055 | 1.0055 | 502.75 | 1461 | 10 | https://octopart-clicks.com/click/track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
5 | MC74HC595ADTR2G | ON Semiconductor | MC74HC595ADTR2G | https://octopart.com/mc74hc595adtr2g-on+semiconductor-501026 | U1, U2, U3, U4, U5 |  | IC SHIFT REGSTR 8BIT 3ST 16TSSOP | 2500 | MC74HC595ADTR2GOSTR-ND | MC74HC595ADTR2G | 29M8105 | Tape & Reel |  | Tape & Reel | 0.12342 | 0.116 | 0.11 | 30000 | 18122 | 35000 | 2500 | 1 | 2500 | /click/track?url=http%3A%2F%2Fwww.digikey.com%2Fproduct-detail%2Fen%2FMC74HC595ADTR2G%2FMC74HC595ADTR2GOSTR-ND%2F919258&ppid=501026&sig=0d40702&sid=459&ct=offers | /click/track?url=http%3A%2F%2Fwww.mouser.com%2FSearch%2FProductDetail.aspx%3Fqs%3Dqg33o%25252b8vzFrYsLNJK%252fAr6Q%253d%253d%26utm_source%3Dmousersearchapi%26utm_medium%3Dapi-aggregator%26utm_campaign%3DMC74HC595ADTR2G%26utm_term%3DMC74HC595ADTR2G%26utm_content%3DON+Semiconductor&ppid=501026&sig=05e7077&sid=2401&ct=offers | /click/track?url=http%3A%2F%2Fwww.newark.com%2F29M8105&ppid=501026&sig=0a16c06&sid=2402&ct=offers | Avnet Express | MC74HC595ADTR2G |  | 0.0669 | 0.3345 | 167.25 | 235000 | 2500 | https://octopart-clicks.com/click/track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
1 | CAT24C256WI-GT3 | ON Semiconductor | CAT24C256WI-GT3 | https://octopart.com/cat24c256wi-gt3-on+semiconductor-46653749 | U18 |  | IC EEPROM 256KBIT 400KHZ 8SOIC | 500 | CAT24C256WI-GT3OSCT-ND |  | 08R5412 | Cut Tape |  | Cut Tape | 0.33936 |  | 0.25 | 7635 |  | 1026 | 1 |  | 1 | /click/track?url=http%3A%2F%2Fwww.digikey.com%2Fproduct-detail%2Fen%2FCAT24C256WI-GT3%2FCAT24C256WI-GT3OSCT-ND%2F2704982&ppid=46653749&sig=0c5a706&sid=459&ct=offers |  | /click/track?url=http%3A%2F%2Fwww.newark.com%2F08R5412&ppid=46653749&sig=088d7d2&sid=2402&ct=offers | Chip One Stop | ONSM-0046246 | Cut Tape | 0.237 | 0.237 | 118.5 | 2627 | 10 | https://octopart-clicks.com/click/track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
2 | RT8268GFP | Richtek | RT8268GFP | https://octopart.com/rt8268gfp-richtek-19674396 | U10, U6 |  | IC REG BUCK ADJ 2A 10MSOP | 1000 | 1028-1045-1-ND |  |  | Cut Tape |  |  | 0.30888 |  |  | 1770 |  |  | 1 |  |  | https://octopart-clicks.com/click/track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 |  |  | element14 APAC | 2341376 | Cut Tape | 0.2913501534 | 0.5827003068 | 291.3501534 | 151 | 1 | https://octopart-clicks.com/click/track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
14 | M74VHC1GT126DF1G | ON Semiconductor | M74VHC1GT126DF1G | https://octopart.com/m74vhc1gt126df1g-on+semiconductor-1229339 | IC3, IC4, IC6, IC7, IC8, IC9, IC10, IC11, IC13, IC14, IC16, IC17, IC18, IC19 |  | M74VHC1GT126DF1G | 7000 | M74VHC1GT126DF1GOSTR-ND | M74VHC1GT126DF1G | 83H7593 | Tape & Reel |  | Cut Tape | 0.0506 | 0.051 | 0.037 | 0 | 12970 | 25985 | 3000 | 1 | 1 | /click/track?url=http%3A%2F%2Fwww.digikey.com%2Fproduct-detail%2Fen%2FM74VHC1GT126DF1G%2FM74VHC1GT126DF1GOSTR-ND%2F1476994&ppid=1229339&sig=02b90c5&sid=459&ct=offers | /click/track?url=http%3A%2F%2Fwww.mouser.com%2FSearch%2FProductDetail.aspx%3Fqs%3D3JMERSakebrJgsZp0Sx%252fsQ%253d%253d%26utm_source%3Dmousersearchapi%26utm_medium%3Dapi-aggregator%26utm_campaign%3DM74VHC1GT126DF1G%26utm_term%3DM74VHC1GT126DF1G%26utm_content%3DON+Semiconductor&ppid=1229339&sig=0a84bce&sid=2401&ct=offers | /click/track?url=http%3A%2F%2Fwww.newark.com%2F83H7593&ppid=1229339&sig=0d098e4&sid=2402&ct=offers | Future Electronics | M74VHC1GT126DF1G |  | 0.0254 | 0.3556 | 177.8 | 0 | 1 | https://octopart-clicks.com/click/track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
1 | CD4050BDR | Texas Instruments | CD4050BDR | https://octopart.com/cd4050bdr-texas+instruments-7092871 | U19 |  | CD4050, 18V tolerant buffer | 500 | 296-31503-1-ND | CD4050BDR | 85X4386 | Cut Tape |  |  | 0.177 | 0.177 | 0.137 | 14638 | 4540 | 0 | 1 | 1 |  | /click/track?url=http%3A%2F%2Fwww.digikey.com%2Fproduct-detail%2Fen%2FCD4050BDR%2F296-31503-1-ND%2F3505786&ppid=7092871&sig=0412955&sid=459&ct=offers | /click/track?url=http%3A%2F%2Fwww.mouser.com%2FSearch%2FProductDetail.aspx%3Fqs%3DUFeyouyReuFMfE96QiKN%252fQ%253d%253d%26utm_source%3Dmousersearchapi%26utm_medium%3Dapi-aggregator%26utm_campaign%3DCD4050BDR%26utm_term%3DCD4050BDR%26utm_content%3DTexas+Instruments&ppid=7092871&sig=0d6da59&sid=2401&ct=offers | https://octopart-clicks.com/click/track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 | Newark | 85X4386 |  | 0.137 | 0.137 | 68.5 | 0 |  | https://octopart-clicks.com/click/track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
10 | RL1220S-R10-F | Susumu | RL1220S-R10-F | https://octopart.com/rl1220s-r10-f-susumu-981945 | R1, R2, R3, R4, R7, R8, R9, R10, R29, R30 |  | RES .10 OHM 1/3W 1% 0805 SMD | 5000 | RL12S.10FTR-ND | RL1220S-R10-F | 28K1609 | Tape & Reel |  | Tape & Reel | 0.03308 | 0.041 | 0.032 | 175000 | 8214 | 10000 | 5000 | 1 | 5000 | /click/track?url=http%3A%2F%2Fwww.digikey.com%2Fproduct-detail%2Fen%2FRL1220S-R10-F%2FRL12S.10FTR-ND%2F432480&ppid=981945&sig=0c9765a&sid=459&ct=offers | /click/track?url=http%3A%2F%2Fwww.mouser.com%2FSearch%2FProductDetail.aspx%3Fqs%3DnCAm%25252bcMdy9yRFRQlDzuLOw%253d%253d%26utm_source%3Dmousersearchapi%26utm_medium%3Dapi-aggregator%26utm_campaign%3DRL1220S-R10-F%26utm_term%3DRL1220S-R10-F%26utm_content%3DSusumu&ppid=981945&sig=08be609&sid=2401&ct=offers | /click/track?url=http%3A%2F%2Fwww.newark.com%2F28K1609&ppid=981945&sig=06c4597&sid=2402&ct=offers | Area51 | RL1220S-R10-F |  | 0.004 | 0.04 | 20 | 2128 |  | https://octopart-clicks.com/click/track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
5 | RC1005J2R2CS | Samsung | RC1005J2R2CS | https://octopart.com/rc1005j2r2cs-samsung-14434021 | R52, R53, R59, R70, R71 |  | RES SMD 2.2 OHM 5% 1/16W 0402 | 2500 | 1276-4313-1-ND |  |  | Cut Tape |  |  | 0.00185 |  |  | 18425 |  |  | 1 |  |  | https://octopart-clicks.com/click/track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 |  |  | Digi-Key | 1276-4313-1-ND | Cut Tape | 0.00185 | 0.00925 | 4.625 | 18425 | 1 | https://octopart-clicks.com/click/track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
31 | RC0402JR-0747KL | Yageo | RC0402JR-0747KL | https://octopart.com/rc0402jr-0747kl-yageo-39834460 | R5, R11, R14, R15, R16, R19, R20, R21, R23, R24, R25, R28, R32, R33, R34, R36, R45, R46, R47, R48, R51, R54, R55, R56, R57, R61, R62, R63, R64, R65, R66 |  | RES 4.7K OHM 1/16W 5% 0402 SMD | 15500 | 311-47KJRTR-ND | RC0402JR-0747KL | 66R1854 | Tape & Reel |  | Tape & Reel | 0.00121 | 0.001 | 0.002 | 770000 | 81188 | 10000 | 10000 | 1 | 10000 | /click/track?url=http%3A%2F%2Fwww.digikey.com%2Fproduct-detail%2Fen%2FRC0402JR-0747KL%2F311-47KJRTR-ND%2F726485&ppid=39834460&sig=0f3564f&sid=459&ct=offers | /click/track?url=http%3A%2F%2Fwww.mouser.com%2FSearch%2FProductDetail.aspx%3Fqs%3DuM1JSSdPjODXwIB%252fG2auqA%253d%253d%26utm_source%3Dmousersearchapi%26utm_medium%3Dapi-aggregator%26utm_campaign%3DRC0402JR-0747KL%26utm_term%3DRC0402JR-0747KL%26utm_content%3DYageo&ppid=39834460&sig=0242ff1&sid=2401&ct=offers | /click/track?url=http%3A%2F%2Fwww.newark.com%2F66R1854&ppid=39834460&sig=044cc80&sid=2402&ct=offers | Wuhan P&S | RC0402JR-0747KL |  | 0.00041 | 0.01271 | 6.355 | 20000 |  | https://octopart-clicks.com/click/track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

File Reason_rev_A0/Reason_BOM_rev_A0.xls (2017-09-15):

Digikey Part nr. | Desc | Ref | QTY 1 | P. ea 1 | P. ext 1 | QTY 500 | P. ea 500 | P. ext 500
Connectors
A19451-ND | CONN HEADER RTANG 3POS .100 TIN | X1 | 1 | 0.14 | 0.14 | 500 | 0.05733 | 28.665
ICs
480-3845-1-ND | SENSOR LINEAR HALL EFFECT | U1 | 1 | 1.48 | 1.48 | 500 | 0.59278 | 296.39
MCP6561UT-E/OTCT-ND | IC COMP PUSH-PULL 1.8V SOT23-5 | U2 | 1 | 0.61 | 0.61 | 500 | 0.39 | 195
Resistors
311-4.7KJRCT-ND | RES 4.7K OHM 1/16W 5% 0402 SMD | R1 | 1 | 0.012 | $0.01 | 500 | $0.00336 | $1.68
490-7102-ND | TRIMMER 10K OHM 0.1W SMD | R2 | 1 | 0.17 | $0.17 | 500 | 0.10998 | $54.99
Capacitors
445-4964-1-ND | CAP CER 0.1UF 25V 10% X5R 0402 | C1 | 1 | 0.04 | 0.04 | 500 | 0.0102 | 5.1
Diodes/LEDs
475-2816-1-ND | LED CHIPLED BLUE 470NM 0603 SMD | LED1 | 1 | 0.21 | 0.21 | 500 | 0.11178 | 55.89
Sum |  |  |  |  | 2.662 |  |  | 1.27543

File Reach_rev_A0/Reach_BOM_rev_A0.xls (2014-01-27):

Digikey Part nr. | Desc | Ref | QTY 1 | P. ea 1 | P. ext 1 | QTY 500 | P. ea 500 | P. ext 500
Connectors
A19450-ND | CONN HEADER RTANG 2POS .100 TIN | X4, X5, X6 | 3 | 0.1 | 0.3 | 1500 | 0.03768 | 56.52
A19451-ND | CONN HEADER RTANG 3POS .100 TIN | X7, X8, X9 | 3 | 0.14 | 0.42 | 1500 | 0.05733 | 85.995
A19452-ND | CONN HEADER RTANG 4POS .100 TIN | X14, X15, X16 | 3 | 0.18 | 0.54 | 1500 | 0.08734 | 131.01
WM7847-ND | CONN HEADER 4POS 5.08MM R/A TIN | X2 | 1 | 1.04 | 1.04 | 500 | 0.648 | 324
WM7953-ND | CONN TERM BLOCK 4POS 5.08MM R/A | X2-2, X20-2 | 1 | 2.5 | 2.5 | 500 | 1.5 | 750
WM7845-ND | CONN HEADER 2POS 5.08MM R/A TIN | X1, X3, X21 | 3 | 0.64 | 1.92 | 1500 | 0.4 | 600
WM7819-ND | CONN TERM BLOCK 2POS 5.08MM | X1-2, X3-2, X21-2 | 3 | 1.43 | 4.29 | 1500 | 0.88794 | 1331.91
S2012EC-23-ND | CONN HEADER .100" DUAL STR 46POS | P8, P9 | 2 | 0.72 | 1.44 | 1000 | 0.41646 | 416.46
ICs
296-28915-5-ND | IC CTRLR STEPPER MOTOR 28HTSSOP | U13, U14, U15 | 3 | 6.53 | 19.59 | 1500 | 3.2625 | 4893.75
CAT24C256WI-GT3OSCT-ND | IC EEPROM 256KBIT 400KHZ 8SOIC | U18 | 1 | 0.71 | 0.71 | 500 | 0.35536 | 177.68
MCP1402T-E/OTCT-ND | IC MOSFET DRIVER 500MA SOT23-5 | U7, U8, U9 | 3 | 0.74 | 2.22 | 1500 | 0.47 | 705
296-4620-1-ND | IC 8BIT SHFT REG TRI-ST 16-TSSOP | U1, U2, U3 | 3 | 0.49 | 1.47 | 1500 | 0.1326 | 198.9
1028-1045-1-ND | IC REG BUCK ADJ 2A 10MSOP | U10 | 1 | 0.76 | 0.76 | 500 | 0.38192 | 190.96
Resistors
RL12S.10FCT-ND | RES .10 OHM 1/3W 1% 0805 SMD | R1, R2, R3, R4, R5, R6 | 6 | 0.32 | 1.92 | 3000 | 0.06306 | 189.18
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

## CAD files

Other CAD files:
PCB_rev_A4A/eagleUp/Untitled.skp

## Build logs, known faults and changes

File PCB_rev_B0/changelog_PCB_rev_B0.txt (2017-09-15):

Changelog Rev A4A -> Rev B0
========================

TODO: 
 - Check BOM against 
 - New Mosfets for fans. Add snubber and flyback. 
 - Skjematikk: polarity protection
	Bruker en ekstra MBRA340T3 i en crowbar-kobling. MÅ TESTES PÅ FORHÅND!
	Alternativ: AON6407, PFET. 
	Dyrere
	Mye effekttap (5mOhm x Vin x Iin)
	Blåser ikke sikringen.
	Reverse polarisation protection (beskyttelse mot å koble + og - motsatt) (P-FET transistor?)

 - CE-godkjenning (innebærer lavere elektromagnetisk støy-nivå, mest sannsynlig 4-lags PCB)	

Done:
 + Skjematikk: 3-pin end stop input connectors (sig, 5v, gnd)
 + Schematics: Added CD4050BD allows for 15 V inputs converted down to 3.3V. 
 + BOM-cost: funnet rimeligere alternativer TI SN74AHC595PW byttes til ON Semi MC74HC595ADTG halv pris: ca 0.21$ til 0.12$
 + Skjematikk: 2-pin thermistor input
 + Skjematikk: mixed-mode pin på stepper-kontrollere
	Bruker 5x M74VHC1GT126 voltage-translating tri-state buffer (.055$ pr stk)
 + Skjematikk: Servo output på endstop_x/y_2
	Bruker 2x M74VHC1GT126
 + Schematics: DAC exchanged with PWM + RC for IREF. 
 + Hardcode EEPROM address to 0x54: Price reduction and board space. 
 + Major League headers: Price reduction
 + Use PWM as DAC: 
	- 1. order low pass filter, R=10K, C=4.7uF gives 17.0mV ripple at 1 KHz. 
	Maximum attainable precision is 3.3V/4096 = 0.8 mV 
   	- http://sim.okawa-denshi.jp/en/PWMtool.php
	- TODO: Increase PWM or use sharper filter. 
 + Blue LED to indicate fuse blown 
 + Larger bulk capacitance. New electrolytic Capacitors (one for each stepper driver)
 + Reverse polarity protection. 
	- MBRA shotky diode. 
 + Remove gate driver on main mosfet. 
	The gate capacitiance of the AON9... is 92pf. 
	With 100 ohm series resitors on the power mosfet gate, the 
	rise time is 60ns giving a slew rate of 500 V/uS. This equates to 
	46 mA maxiumum current drawn. The PCA986 has a maximum current source capacity of 
	10 mA, giving a maxiumum slew rate of 100 V/uS which gives a power dissipation 
	of ?? W at 180W load with a PWM frequency of 1 KHz. 
 + Remove 4.7K res on address of PCA986. 
	- Price and board space reduction
	- This is given as example in PCA986 datasheet. 
 + New DRV8825 layout
	- Lower audible noise level on steppers. 
	- Better heat dissipation (enables higher max current, cooler running)
 + PWM for servos from BBB. 
 + Four pin connector on end stop Z2 adds 12V for magnetic resonance sensor. 
 + New Capacitors: Better capacitance at higher voltage. 
 + New low power mos fets: End of life, lower price smaller footprint. 
 + Less BOM lines 
 + 500 ohm series resistors = 10 mA on all mos fets. 
 + Use free pin on shift registers to enable servo outputs
 + Make sure heaters are turned off in case of kernel panic. 
	- Using BBB watchdog in conjunction with enable pin on P9.41. 

NOTES: 
Stepper drivers: 
 - TMC2100: $2.5
   + Cheaper
   + More buzz. 
   - Tristate configurations. 
   -  
 - DRV8825: $2.7
   + Layout finished. 

Enable PWM:
Trigger kernel panic

echo 116 > /sys/class/gpio/export 
echo out > /sys/class/gpio/gpio116/direction
echo 1 > /sys/class/gpio/gpio116/value 
echo c > /proc/sysrq-trigger

A kernel panic will keep the GPIO in its current state...
We need some sort of watchdog timer. 
 - Solution: Use the built in watchdog timer on BBB. 

Gate driver removal:
TODO: sink/source calculations- 

 - Research: programmerbar slew-rate
	digipot med lav nok resistans + høy nok operating voltage til å settes mellom gate driver og mosfet ser ikke ut til å finnes
 - Lavere støynivå på Mosfetene, muligens programmerbar slew-rate. 

ADC precicion calculations: 
 - 12 bit ADC, 1.8V range: 1.8/4096 = 439uV pr bit. 
 - Oversampling

Mixed mode current decay: 
 - Internal pullups/pulldowns are 130K/80K in DRV8825, 
   so external pullups/pulldowns of 4.7K/4.7K should place the
   pin floating at 3.3V/2. 

Concerns: 
 - 3.3V logic input although buffers are using 5V VCC. 
 - ADC filtering: Should I use GND_ANA or GND_D? 
 - Low power mosfets, flyback diode? Snubber?
 - Capacitance for fans? 
 - Schotky diode for reverse polarisation.

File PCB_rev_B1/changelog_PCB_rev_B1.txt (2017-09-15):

Changelog Rev A4A -> Rev B1
========================

Done:
 + 3-pin end stop input connectors 
	- The chosen pin config (sig, 5v, gnd) is compatible with servos. 
	- Except Z2 which also has 12V available: (sig, 5V, gnd, 12V)
 + Added CD4050BD allows for 15 V inputs on all end stop inputs
 + 2-pin thermistor input
 + Servo output on endstop x2 / y2
	Using 2x M74VHC1GT126
 + Hardcode EEPROM address to 0x54
	- Price reduction and board space. 
 + Major League headers: 
	- Price reduction
 + DAC exchanged with PWM + RC for IREF. 
	- 1. order low pass filter, R=10K, C=4.7uF gives 13.0mV ripple at 1 KHz. 
	Maximum attainable precision is 2.5/4096 = 0.61 mV 
   	- Online tool: http://sim.okawa-denshi.jp/en/PWMtool.php
	- TODO: Increase PWM or use sharper filter. 
 + Blue LED to indicate fuse blown 
	- Price reduction (BOM lines)
 + Larger bulk capacitance. 
	- New electrolytic Capacitors (one for each stepper driver)
 + Reverse polarity protection. 
	- MBRA shotky diode. 
 + Remove gate driver on main mosfet. 
	The gate capacitiance of the AON6758 is 92pf. 
	With 100 ohm series resitors on the power mosfet gate, the 
	rise time is 60ns giving a slew rate of 500 V/uS. This equates to 
	46 mA maxiumum current drawn. The PCA986 has a maximum current source capacity of 
	10 mA, giving a maxiumum slew rate of 109 V/uS which gives a power dissipation 
	of 3? W at 180W load with a PWM frequency of 1 KHz. 
 + Remove 4.7K res on address of PCA986. 
	- Price and board space reduction
	- This is given as example in PCA986 datasheet. 
 + New stepper drivers: TMC2100
	- Lower audible noise level on steppers. 
 + PWM for servos from BBB. 
 + Four pin connector on end stop Z2 adds 12V for magnetic resonance sensor. 
 + New Capacitors: Better capacitance at higher voltage. 
 + New low power mos fets: End of life, lower price smaller footprint. 
 + Less BOM lines 
 + 500 ohm series resistors = 10 mA on all mosfets. 
 + Use free pin on shift registers to enable servo outputs
 + Make sure heaters are turned off in case of kernel panic. 
	- Using BBB watchdog in conjunction with enable pin on P9.41. 
 + Removed External connector since PWM ciurcuit needs to be available on 
	 Reach anyway. Use SPI_CS0 for the shift registers. 

NOTES: 
Stepper drivers: 
 - TMC2100: $2.5
	+ Cheaper
   	+ More configuration options for lower noise. 
   	- Tristate configurations. 

- Reverse Polarity protection on input:
	- Currently using MBRA340T3 in a crowbar connection. 
	Alternative: AON6407, PFET. 
	- More expensive
	- More effect loss (5mOhm x Vin x Iin)
	+ Does not blow the fuse. 

ADC precicion calculations: 
 - 12 bit ADC, 1.8V range: 1.8/4096 = 439uV pr bit. 
 - Oversampling

Concerns: 
 - 3.3V logic input although tri state buffers are using 5V VCC for servos. 
 - ADC filtering: Should I use GND_ANA or GND_D? 
 - Low power mosfets, flyback diode? Snubber? 
	- No, not inductiuve load. (well, it might be but not a large inductive) 
 - Capacitance for fans? 
	- No, not an inductive load/small load 
 - Schotky diode for reverse polarisation. Must test that is can withstand the power until fuse blows. 
 - Mosfet cooling on drain side 

TMC2100 notes: 
 - Layout is based on the exmaple in section 
	16.4 of the datasheet. 
 - External 5V is available, but since it is from a 
	buck regulator, the ripple is probably below 
	the acceptable levels of 5 mV. 
- AIN Iref using PWM: 
	- 2.5V @ 12 bit = 0.61 mV 
	- Datasheet recommends: 22K + 1uF low pass @ 20KHz = 1.4mV ripple 
	20 KHz gives higher 
	- 10K + 4.7uF low pass @ 1K  = 133mV ripple
	- 22K + 4.7uF low pass @ 1K  = 6.0mV ripple
	- 47K + 10 uF low pass @ 1K  = 1.3mV ripple
	- 10K + 4.7uF low pass @ 10K = 1.3mV ripple, using this. 
- DIAG1 - Index output is left unconnected, since it does not offer any 
	value in this application.
- CFG 3 is left open: 
	-External reference voltage on pin AIN. Current scale set by sense resistors and
	scaled by AIN. 

- CFG0 = Chopper off time: High or low. 
- CFG2 = Microstepping: High, low or Open
- CFG1 = Microstepping: High or low. 
- CFG3 = Use Ext. ref.: Open
- CFG4 = Chopper hysteresis: High or Low 
- CFG5 = Chopper blank time: High or low
- CFG6 = Enable: Connected to common enable. 

PWM notes: 
	- Rdson @ 5V = 0.005 ohm
	- Heating element 180 W @ 12 V:  15 A,  R = U/I = 12/15 = 0.8 ohm
	- Effect loss in Mosfet @ fully on: 1.125 W
	- Max effect loss in package: 4.1W
	- Rise time is I/C = 10mA/92pF = 109V/us => rise time is 12/109 = 0.11 uS
	- Time spent switching @ 10KHz: (1.1*10^-7)/(10^-4) ms = 0.11%
	- Assuming linear switching (wrong assumption, but WTH)
	- TODO: calculate Effect loss @ 10KHz
	
 - CE-markings. Not necessary since it is not a consumer product.

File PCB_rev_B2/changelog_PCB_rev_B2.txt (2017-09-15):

Changelog Rev B1 -> Rev B2
========================
 + Removed the pullup-resistors on shift regs.
 + Use a pin to configure enable on steppers. 
 + Pull-downs on small mos-fets.
 + Pull-ups on end-stop inputs.
 + Two stage filter on PWM DAC. 
 + Removed voltage divider on PWM DAC. 
 + 4.7 uF wrong footprint/package
 + Bypass using SYS_5V. 
 + Large servos cause voltage drop disabling the CPU. 
   + Consider using the same DC-DC converter for 5 V.  
 + Add decoupeling caps on tristate regs
 + Update BOM. 
    + Cheaper 40K resistors
    + Better precicion on 10K, 1%
    + 0402 package on 10nF

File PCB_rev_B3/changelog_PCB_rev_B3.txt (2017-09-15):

Changelog Rev B2 -> Rev B3
========================

TODO: 

DONE: 
 + C28 etc. too close. 
 + Change pin-out on end stops. 
 + Change pin-out on Steppers.
 + Remove names from silk screen
 + Exposed thermal vias on the underside of the PCB.  
 + Tri-state buffers on enable steppers to facilitate power down mode. 
 + Wrong voltage divider value for thermistors, 470K instead of 4.7K. 

CONCERNS: 
 - Hot electolytic capaciors. Test with better PSU. 
 - Heaters not in use slightly dim.

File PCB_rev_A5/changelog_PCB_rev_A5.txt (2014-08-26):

Changelog Rev A4A -> Rev A5
========================
- Reverse polarity protection
- Tripple connectors and 5V on end stops
- Input protection on end stops
- Duble connectors on thermistors
- Servo output
- Programmable/trimmable rise time on heaters.

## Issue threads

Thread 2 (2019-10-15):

Gerber File issue

MatthiasPopp, 2019-10-15:
Hi Elias, hi everybody,
first, thank you very much for the awesome work on the replicape.
I checked the gerber (b4 version) after a faulty pcb order and there seem to be an issue.
At location arround 81, 40 (mm) one can see that the b4 version does not pass the DRC. So the Eagle files and the generated gerber cannot be manifactured. (My manifacturer acted to be dumb and just processed the gerbers) Can you confirm that?
I took the time and redesigned the b4 version to be 100 x 70 mm and 2 layer instead of 4. When I get the pcbs I will test them for current capability, thermals  and compatibility and will contribute a pull request
Or am I totaly on the wrong track and the b4 version is not the latest one?
Best regards from Germany,
Matthias

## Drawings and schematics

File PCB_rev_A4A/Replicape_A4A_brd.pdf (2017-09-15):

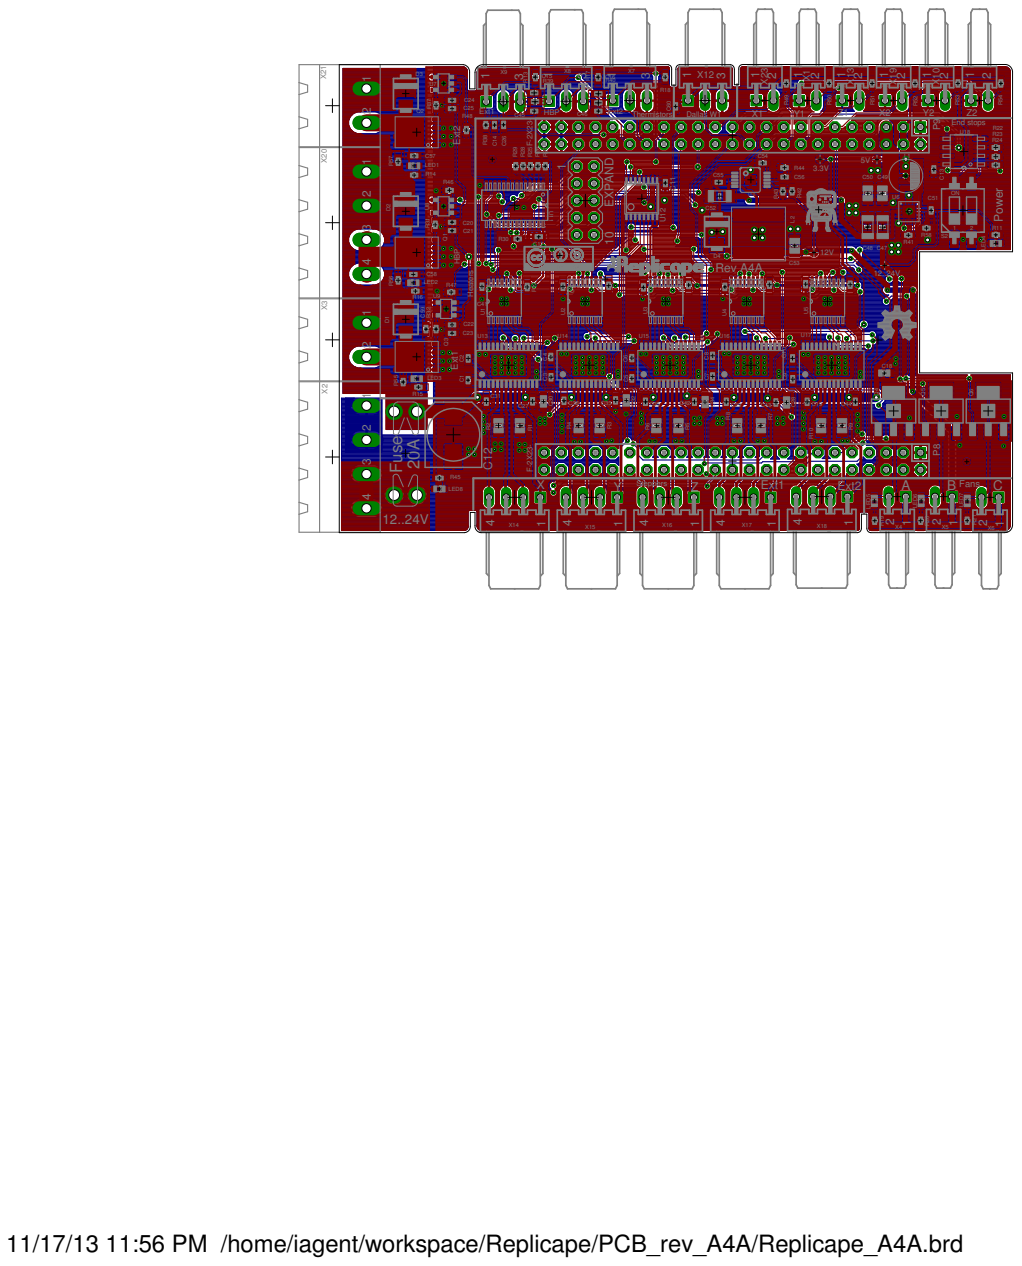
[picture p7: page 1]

11/17/13 11:56 PM /home/iagent/workspace/Replicape/PCB_rev_A4A/Replicape_A4A.brd

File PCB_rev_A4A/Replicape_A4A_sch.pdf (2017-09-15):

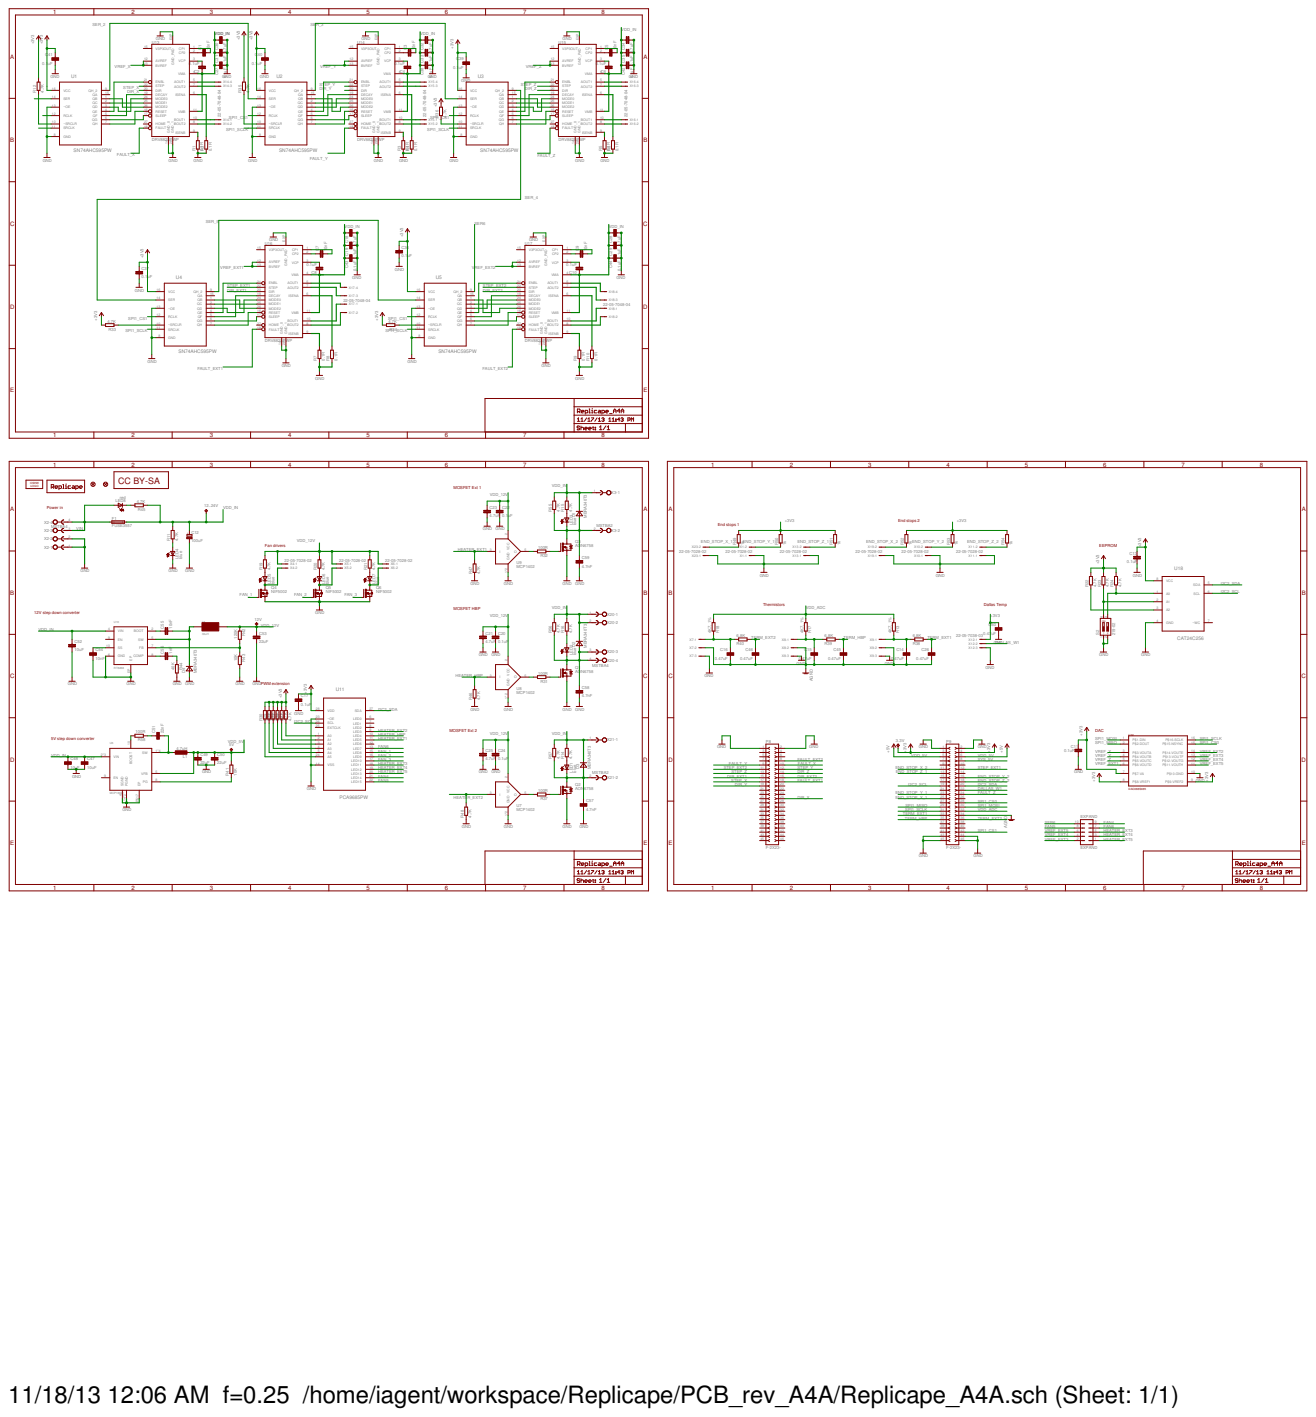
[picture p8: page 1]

blue blue blue GND

11/18/13 12:06 AM f=0.25 /home/iagent/workspace/Replicape/PCB_rev_A4A/Replicape_A4A.sch (Sheet: 1/1)

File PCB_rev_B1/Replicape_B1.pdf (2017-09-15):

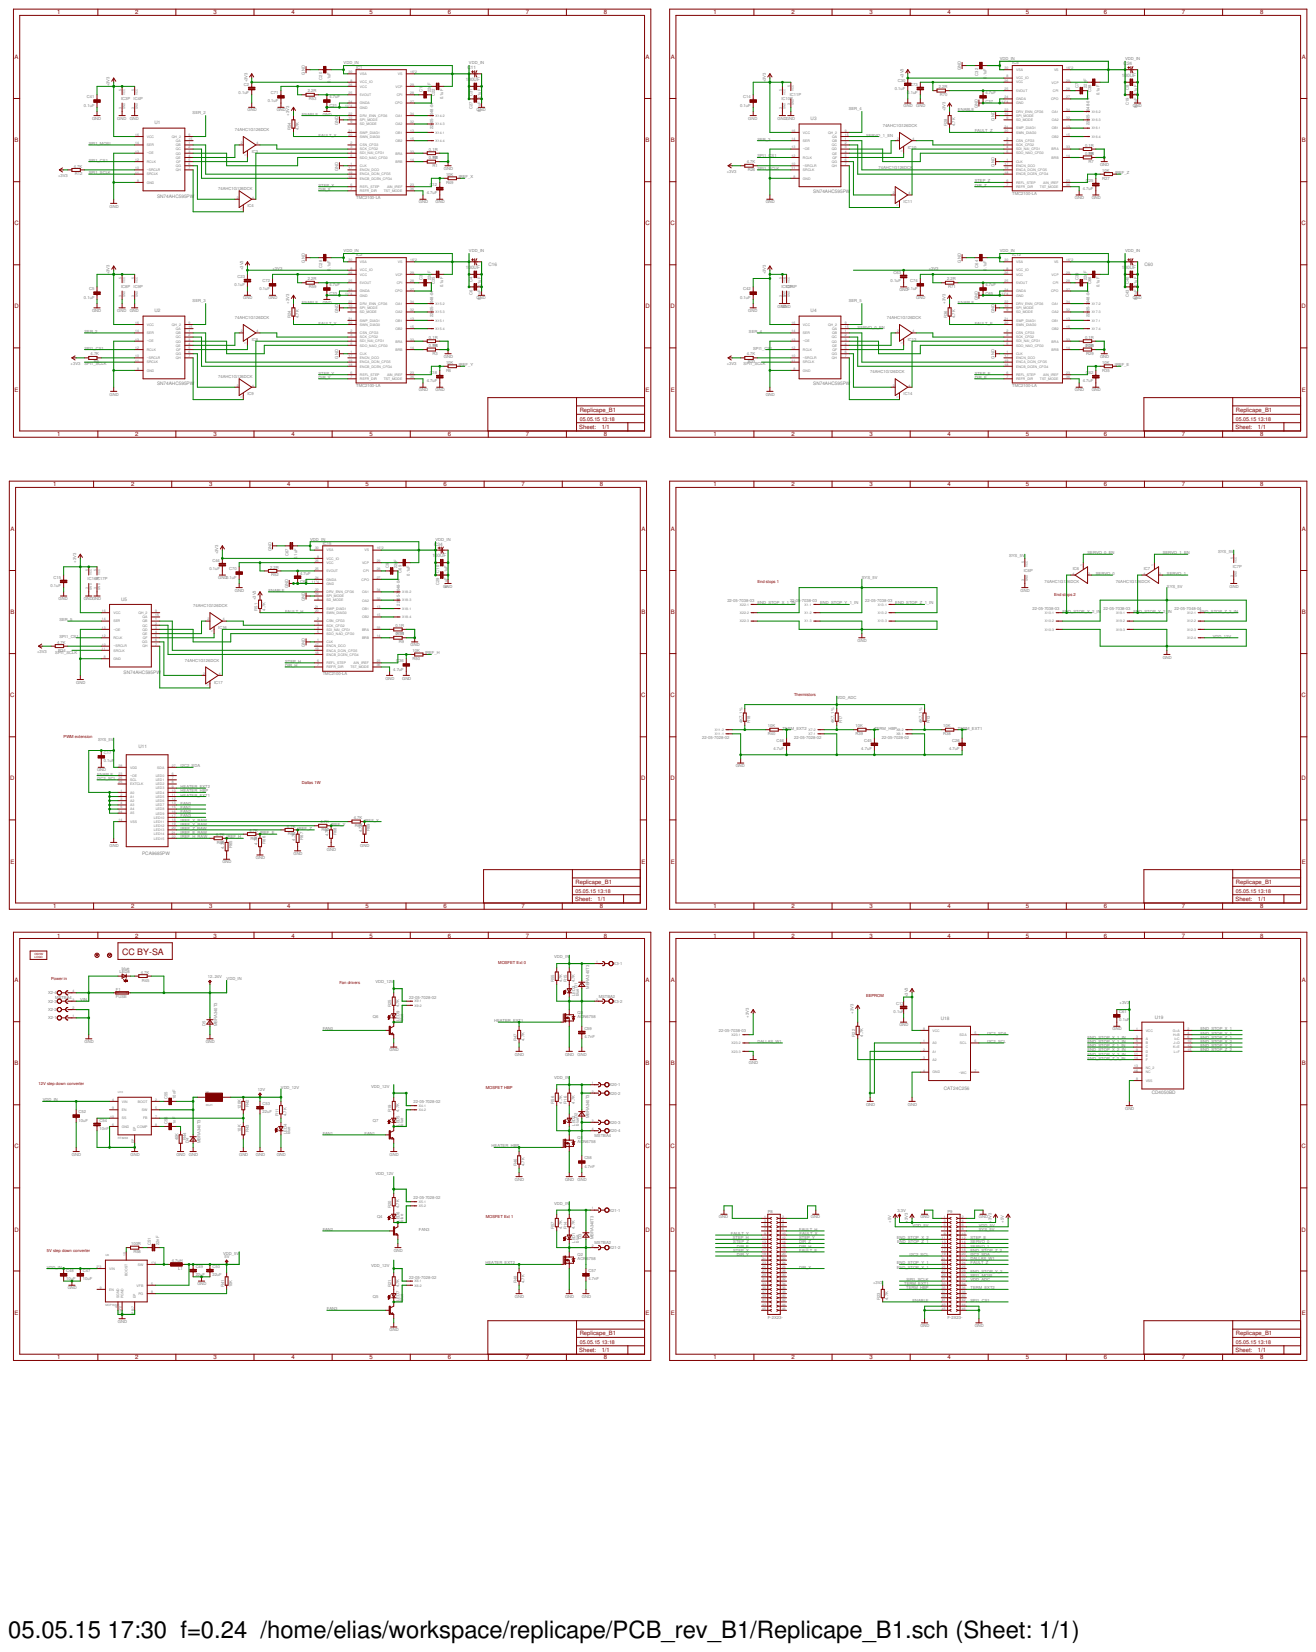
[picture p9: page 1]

blue blue blue GND

05.05.15 17:30 f=0.24 /home/elias/workspace/replicape/PCB_rev_B1/Replicape_B1.sch (Sheet: 1/1)

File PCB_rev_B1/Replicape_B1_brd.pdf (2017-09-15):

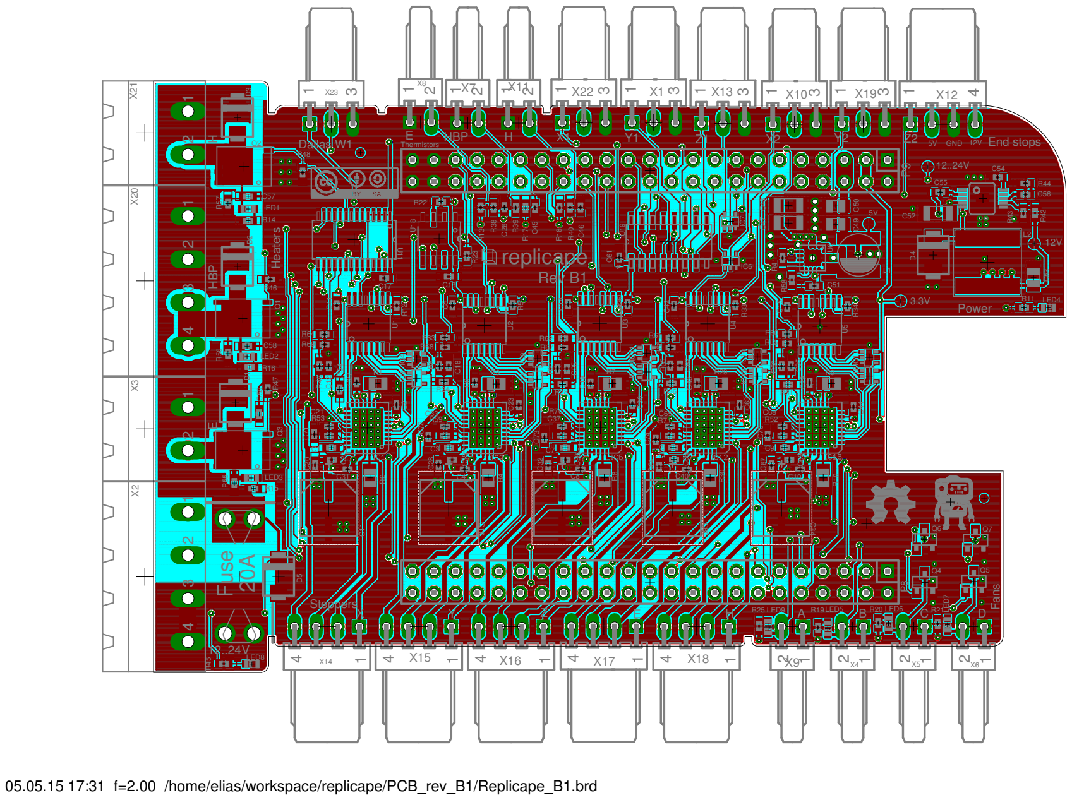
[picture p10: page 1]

05.05.15 17:31 f=2.00 /home/elias/workspace/replicape/PCB_rev_B1/Replicape_B1.brd

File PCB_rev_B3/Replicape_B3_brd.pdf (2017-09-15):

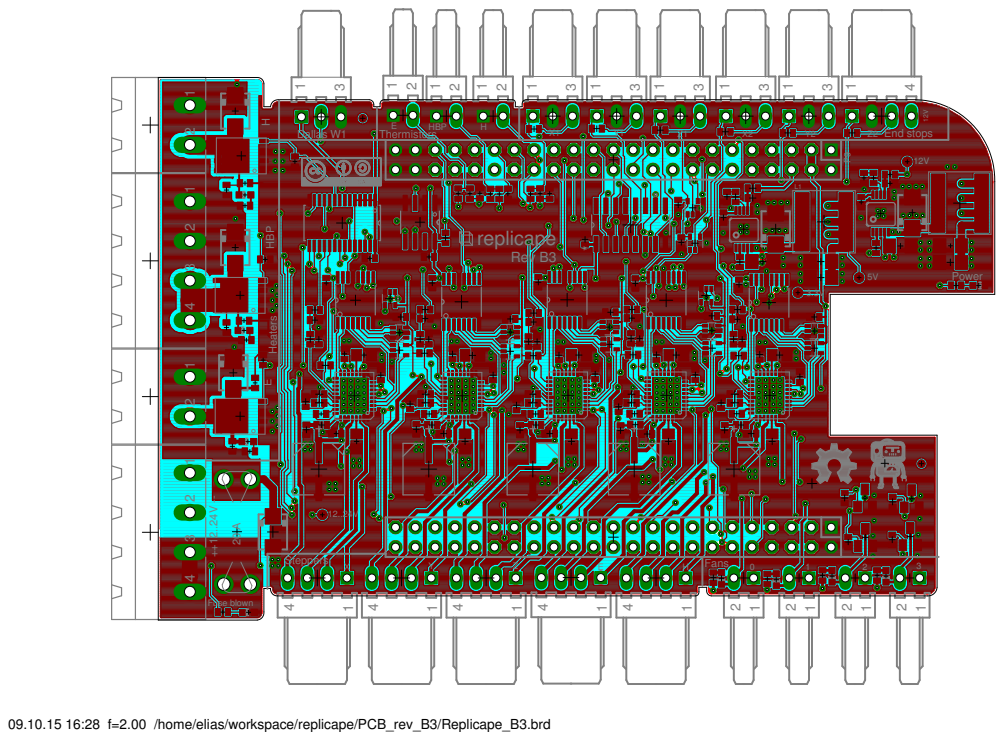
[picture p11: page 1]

09.10.15 16:28 f=2.00 /home/elias/workspace/replicape/PCB_rev_B3/Replicape_B3.brd

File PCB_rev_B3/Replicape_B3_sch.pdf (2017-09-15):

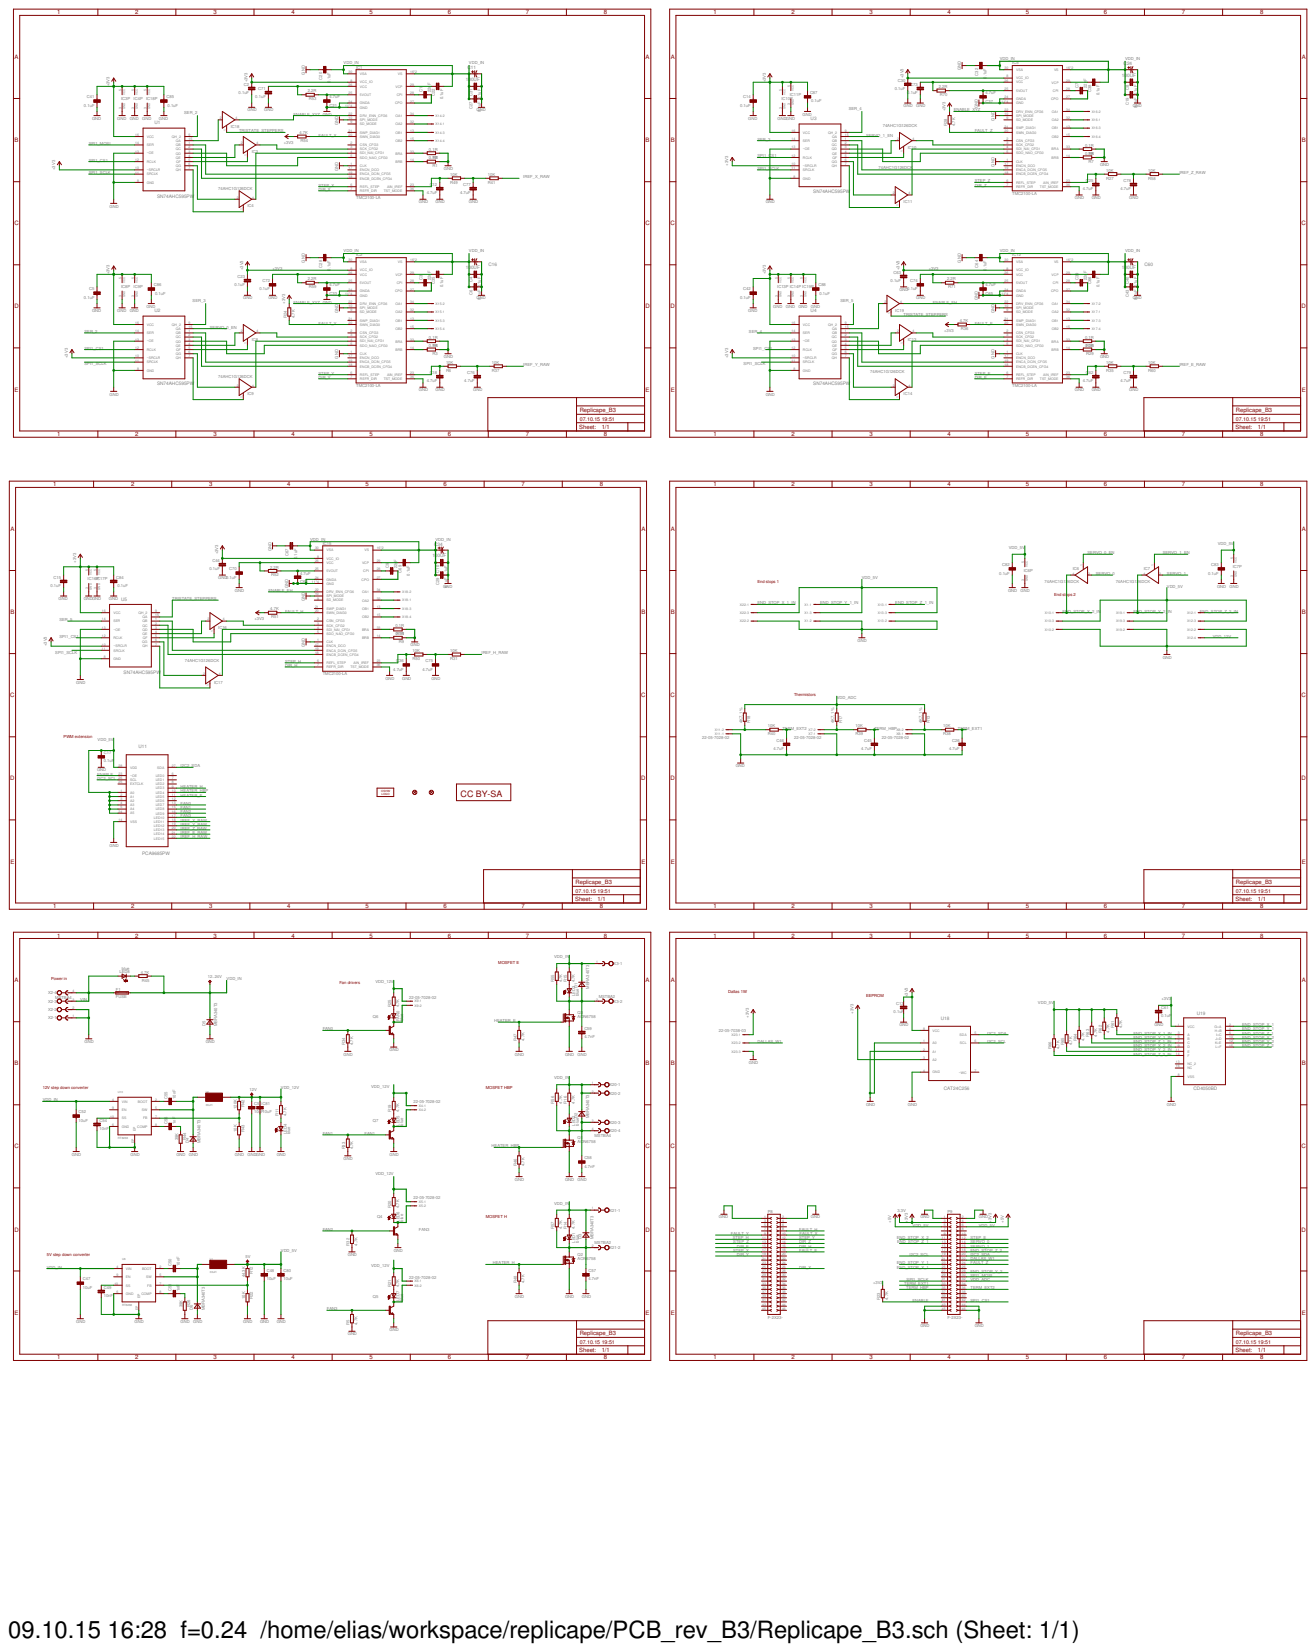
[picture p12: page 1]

blue blue blue GND

09.10.15 16:28 f=0.24 /home/elias/workspace/replicape/PCB_rev_B3/Replicape_B3.sch (Sheet: 1/1)

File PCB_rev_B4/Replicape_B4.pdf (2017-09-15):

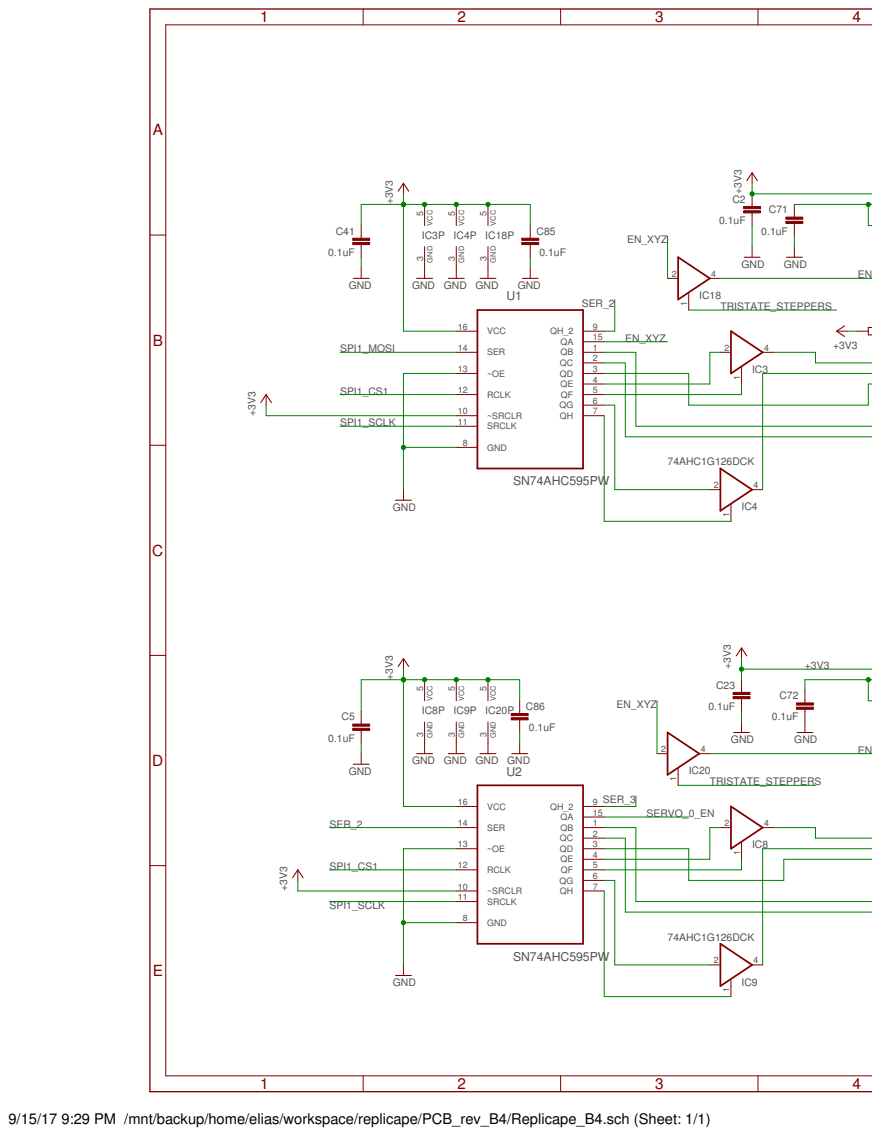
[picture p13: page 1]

9/15/17 9:29 PM /mnt/backup/home/elias/workspace/replicape/PCB_rev_B4/Replicape_B4.sch (Sheet: 1/1)

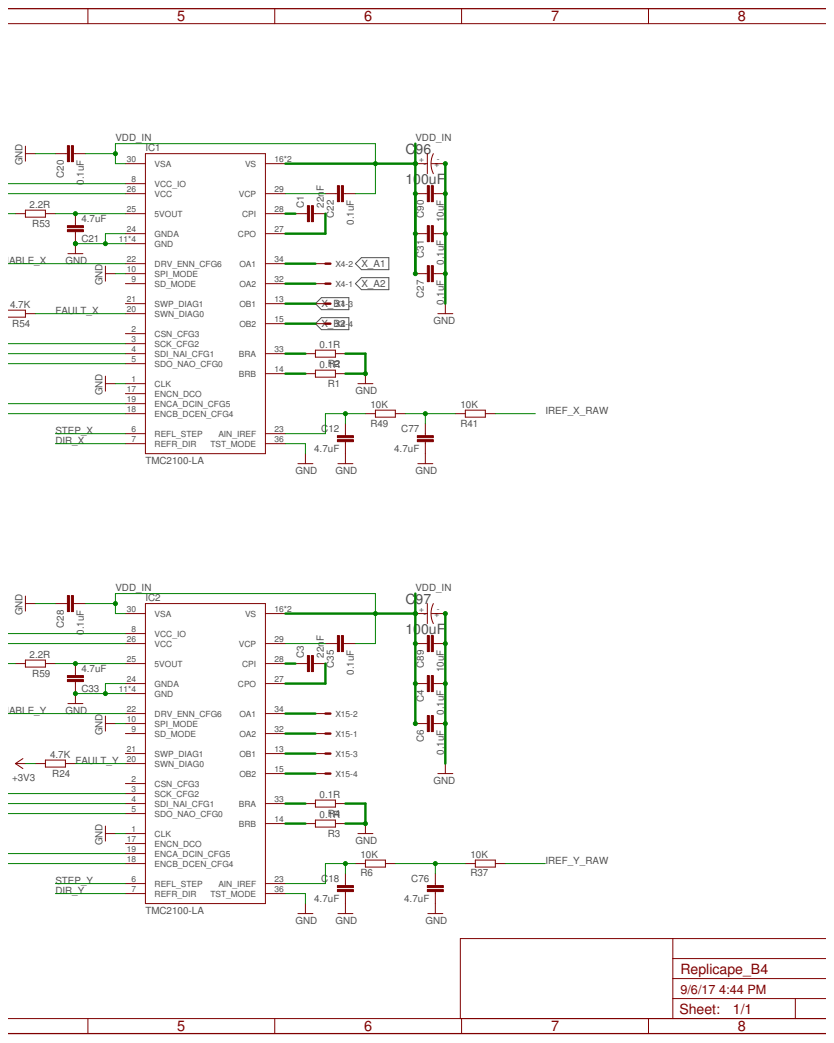
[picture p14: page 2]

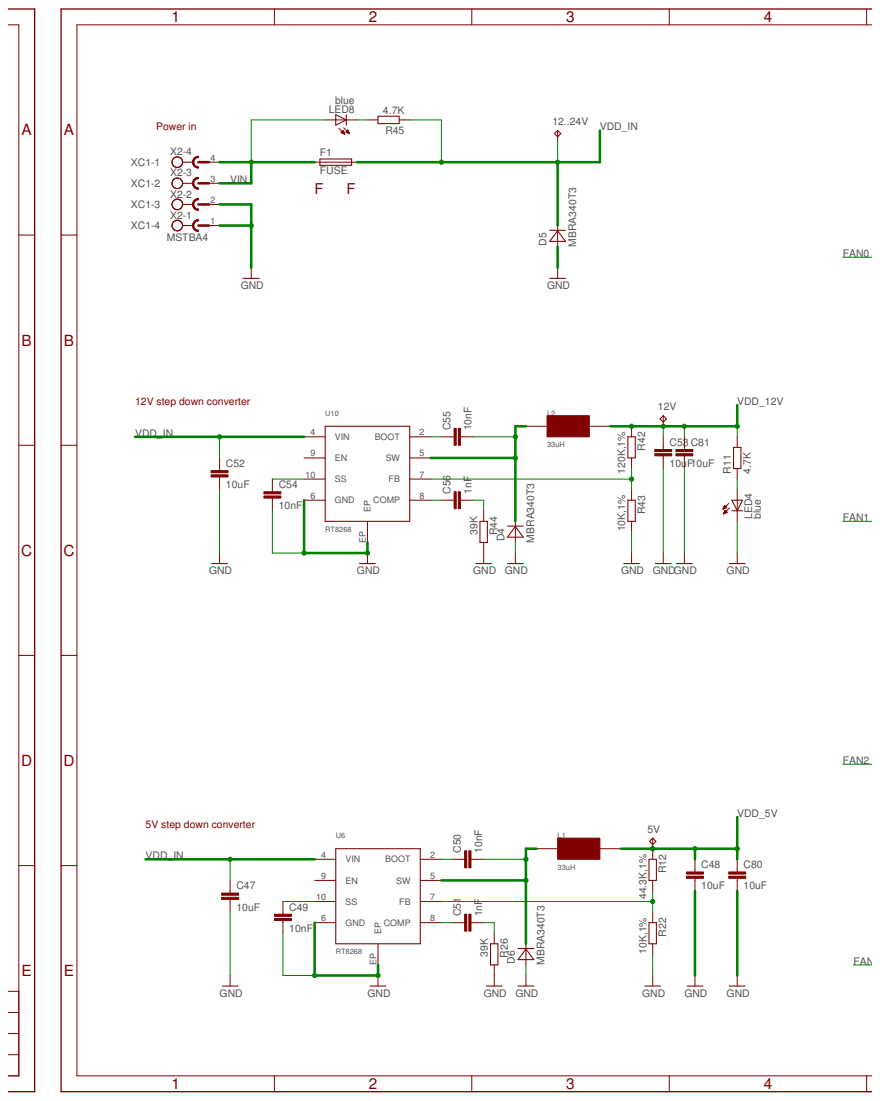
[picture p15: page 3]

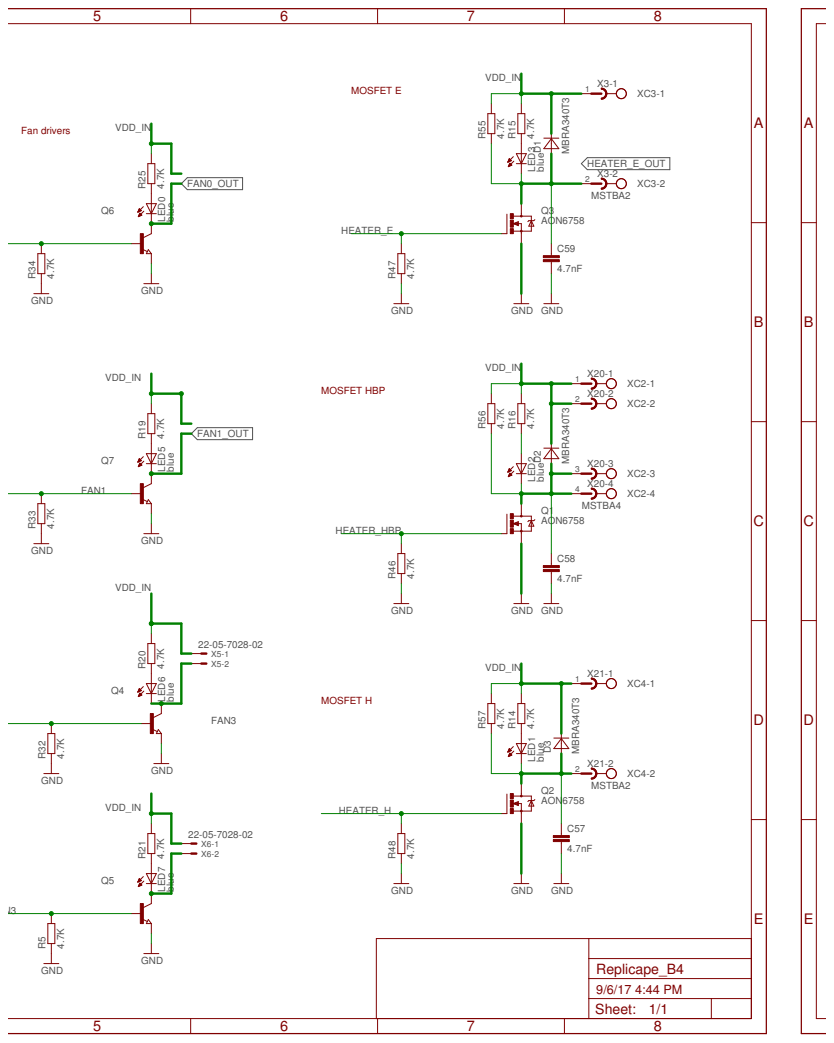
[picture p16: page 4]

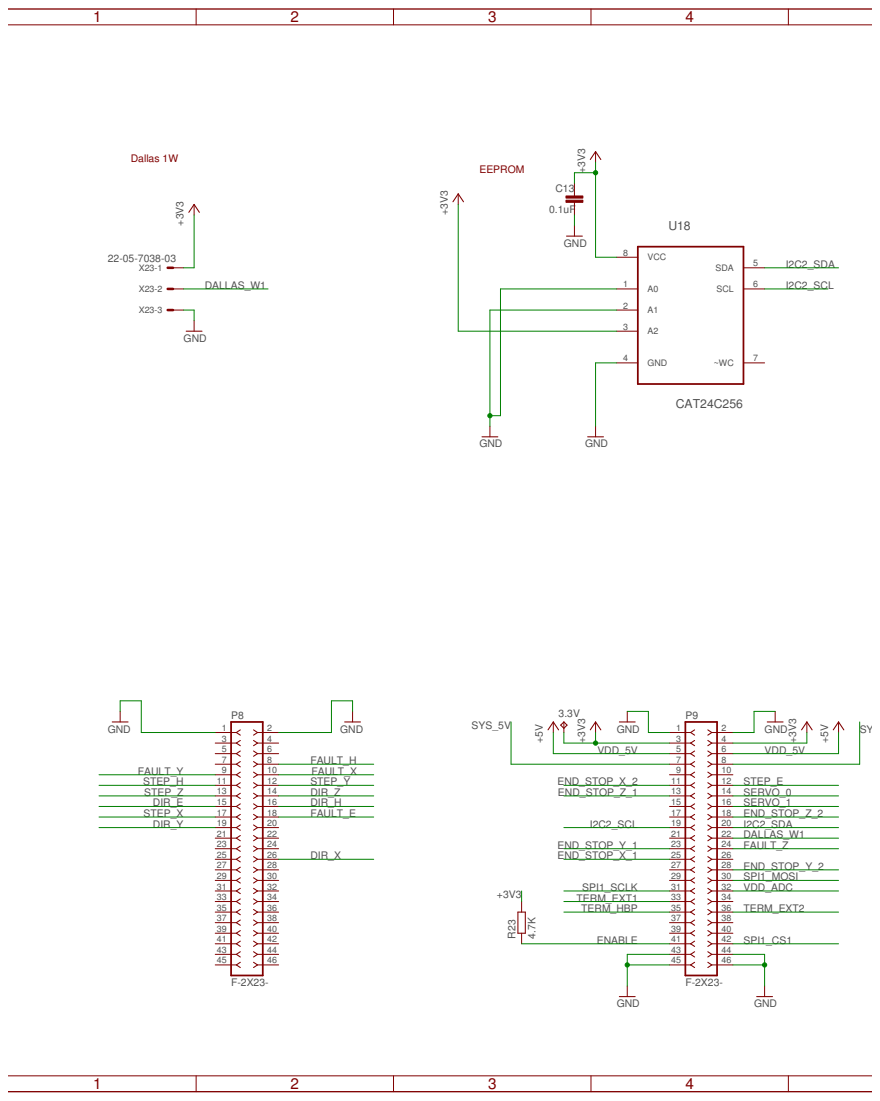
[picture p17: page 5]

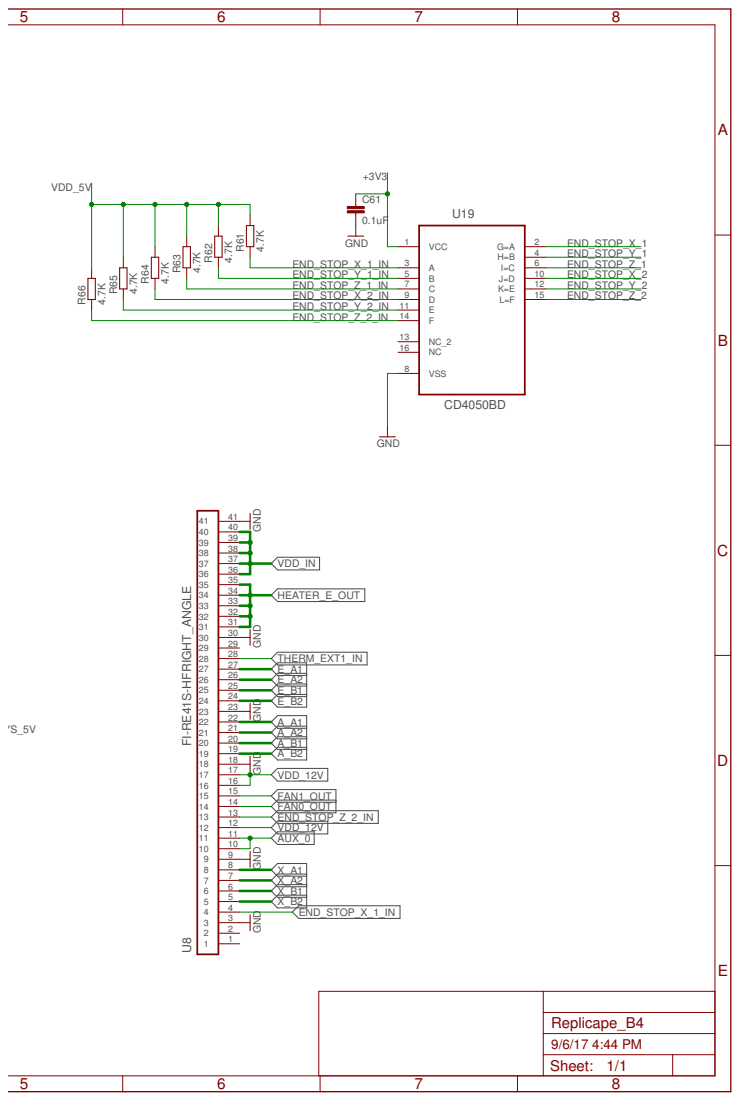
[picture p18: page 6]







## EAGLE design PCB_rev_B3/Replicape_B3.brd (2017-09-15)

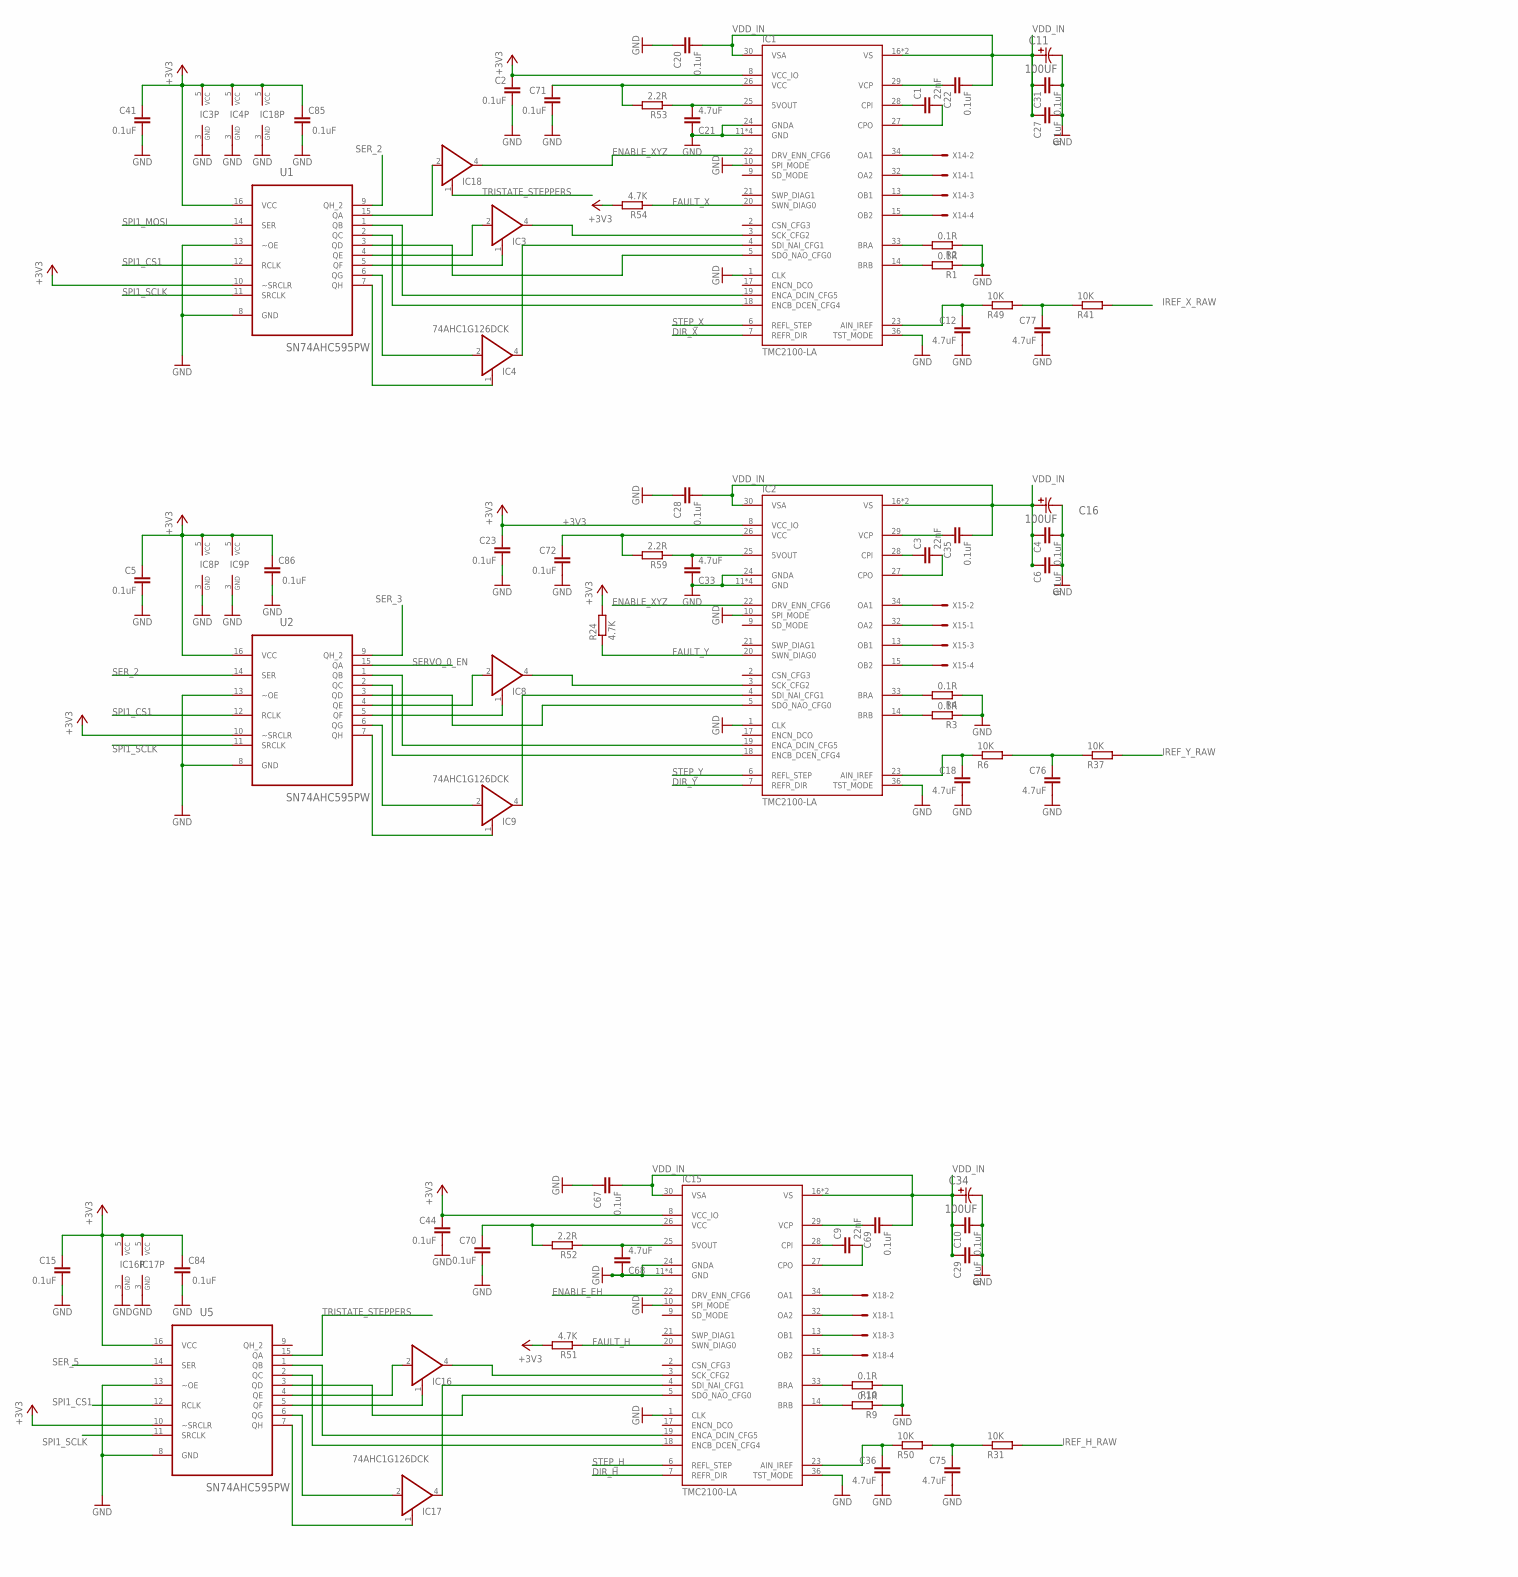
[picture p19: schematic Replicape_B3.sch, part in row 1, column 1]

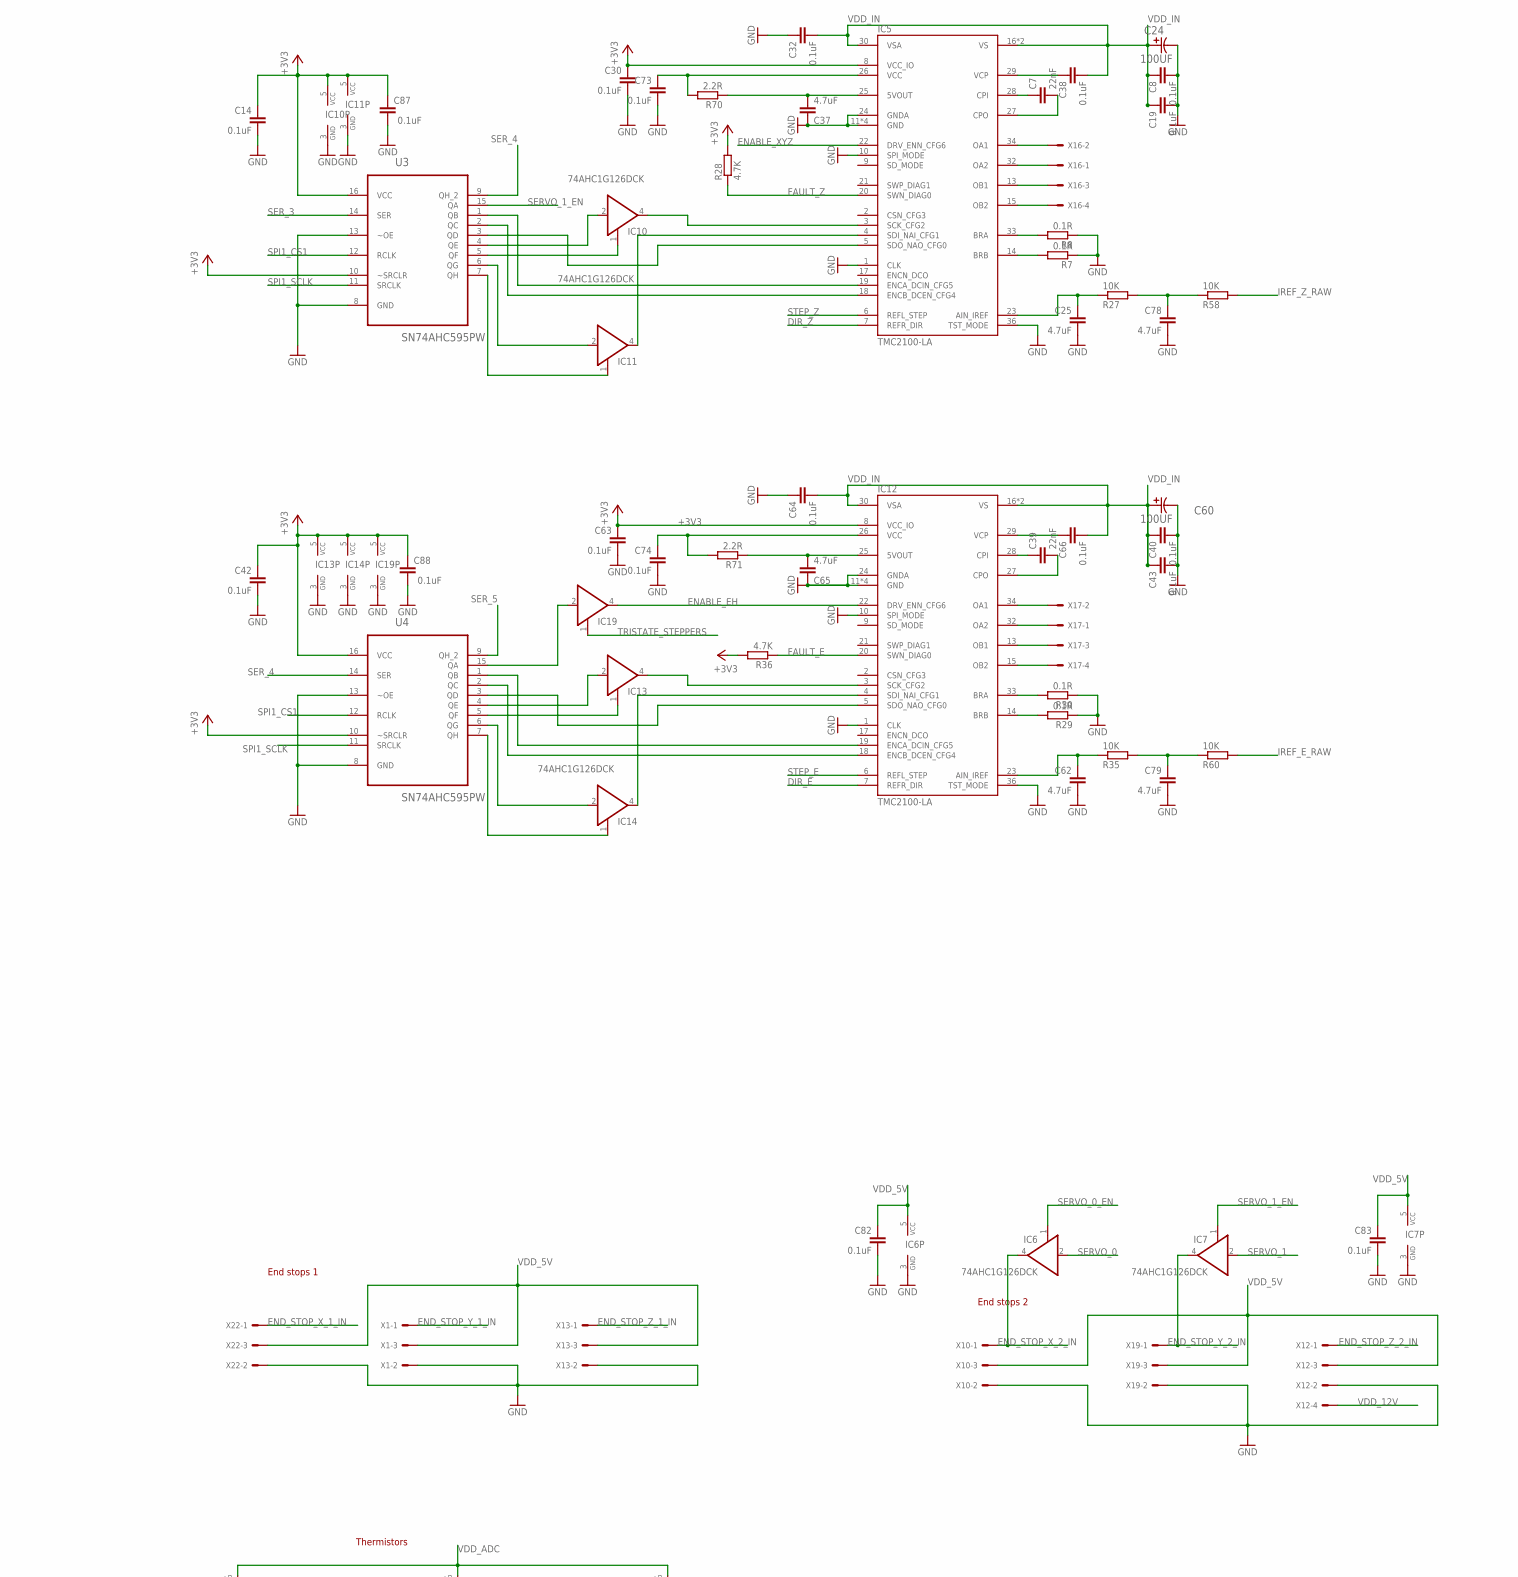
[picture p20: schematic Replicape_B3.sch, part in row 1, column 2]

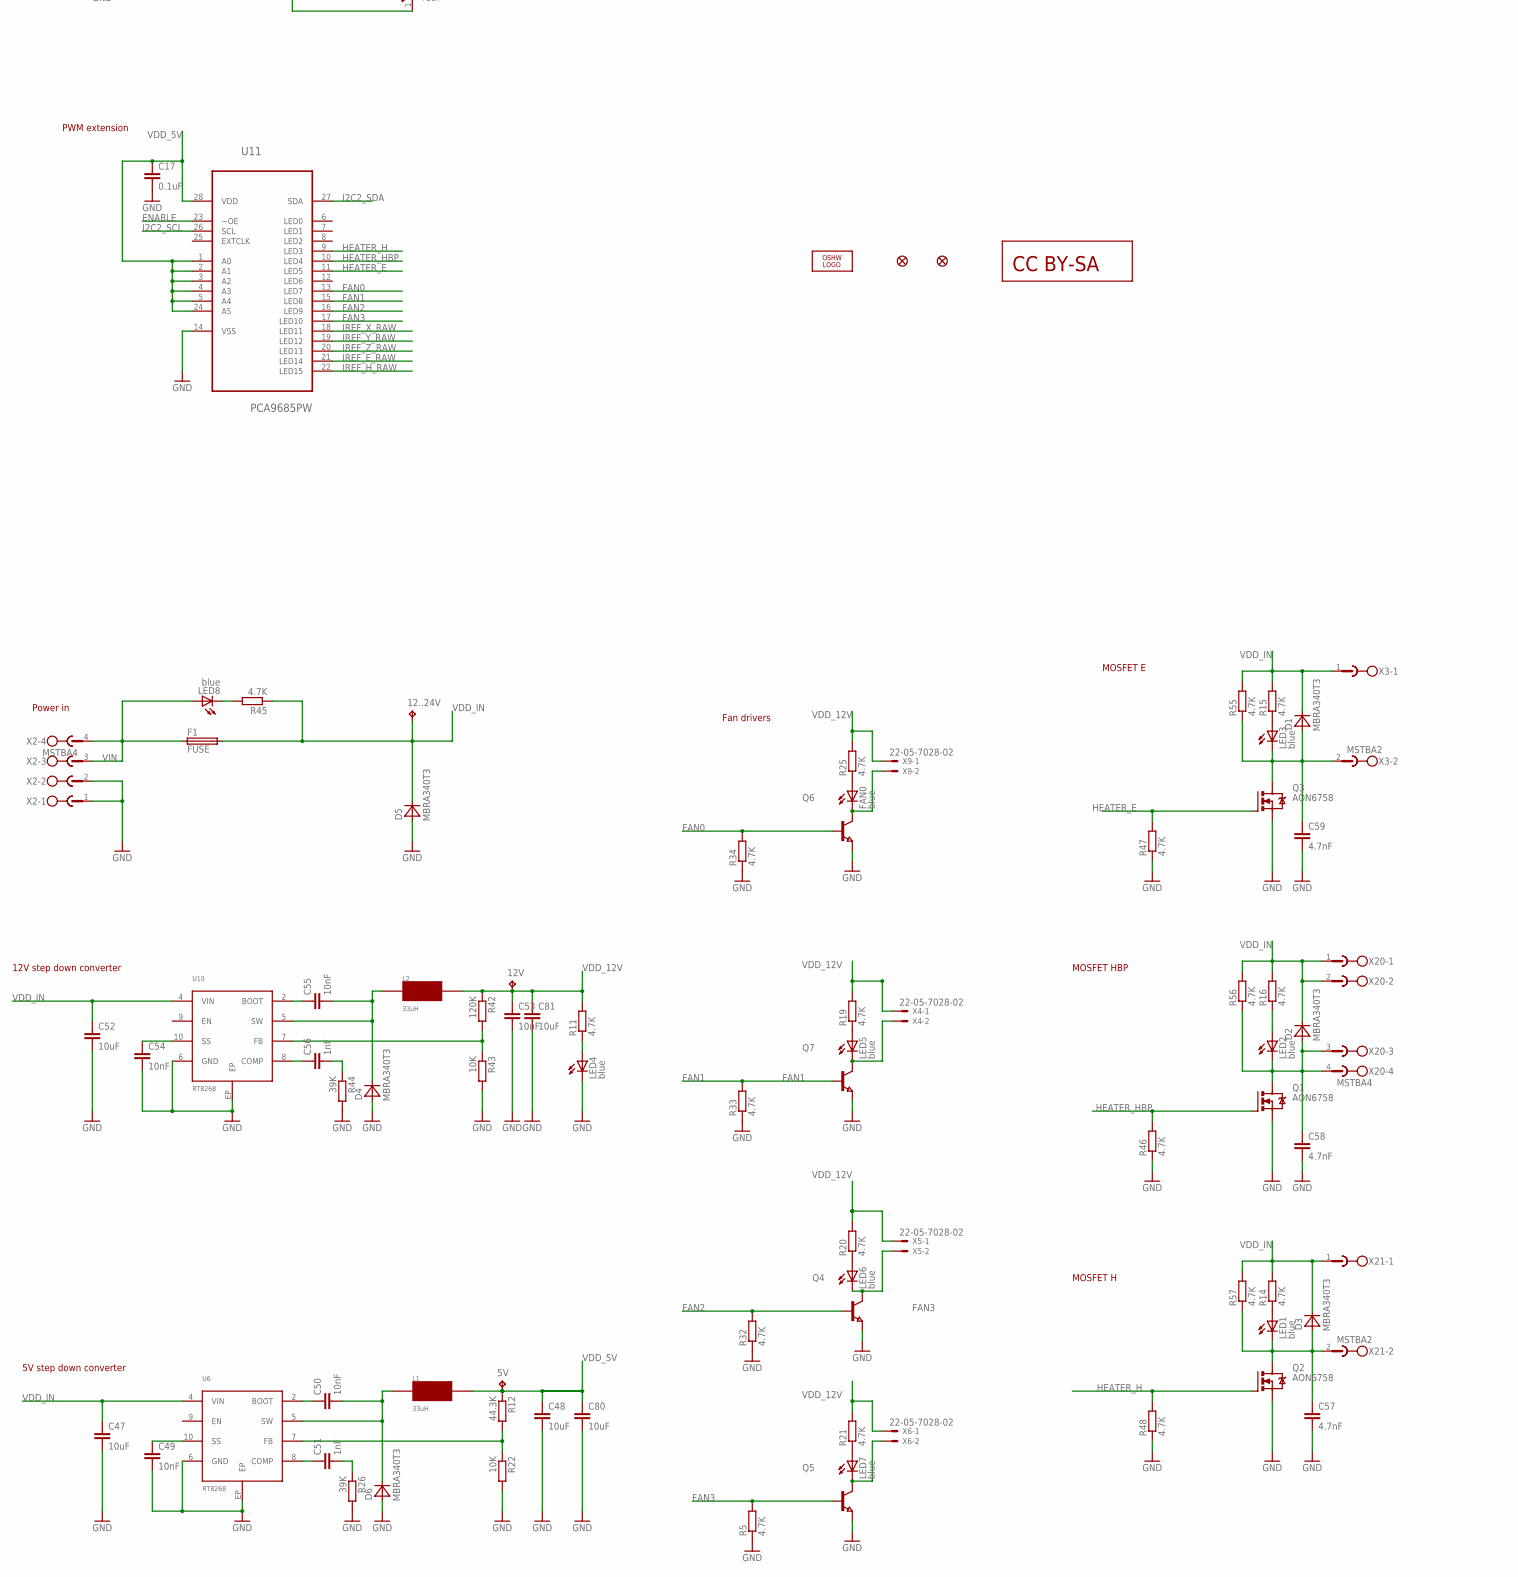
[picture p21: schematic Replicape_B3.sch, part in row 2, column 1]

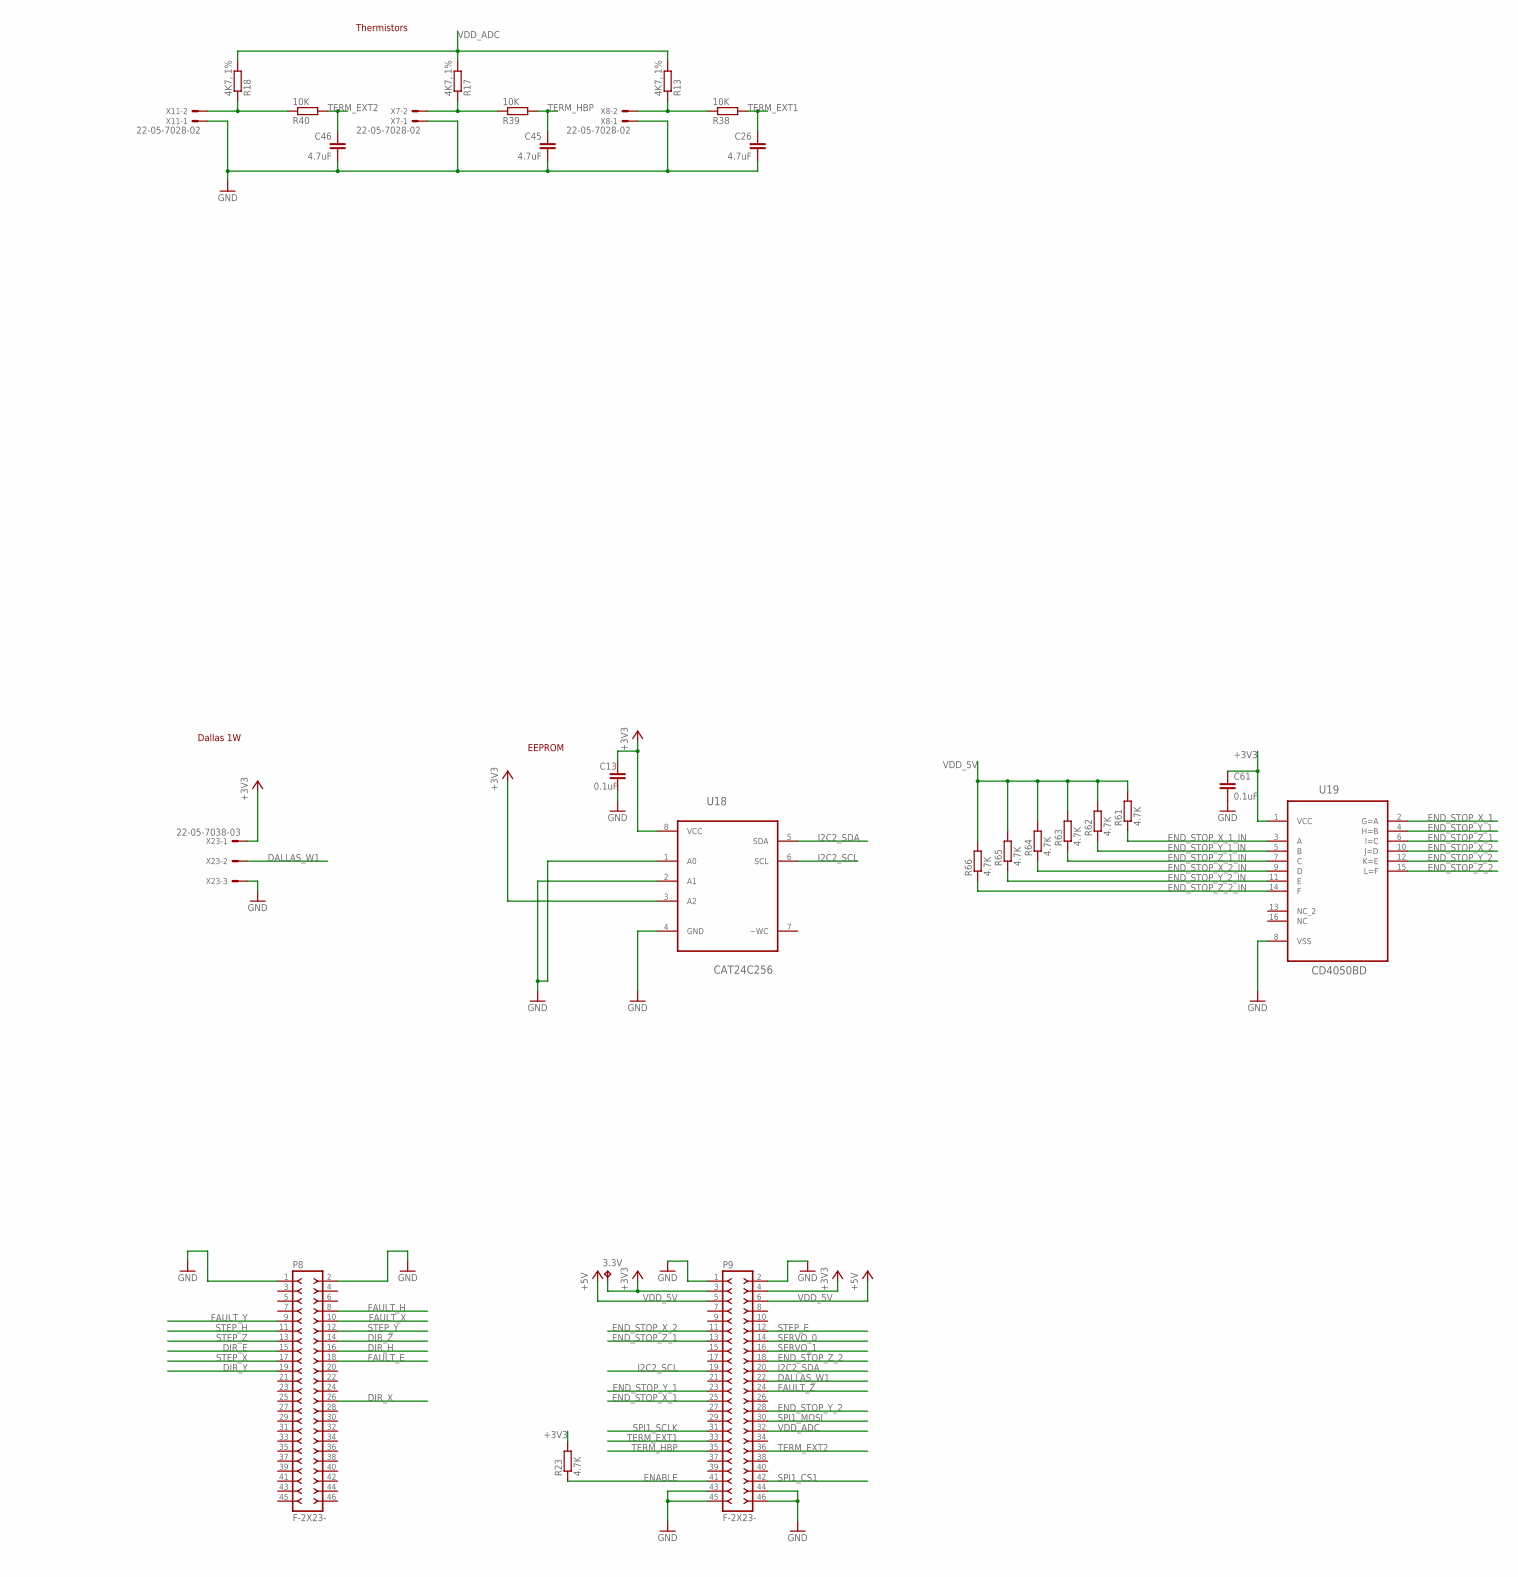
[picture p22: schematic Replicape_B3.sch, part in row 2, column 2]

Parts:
3.3V, 5V, 12..24V, 12V: TPB1,27; B1,27
C1, C3, C7, C9, C39: 22nF; C0402
C2, C4, C5, C6, C8, C10, C13, C14, C15, C17, C19, C20, C22, C23, C27, C28, C29, C30, C31, C32, C35, C38, C40, C41, C42, C43, C44, C61, C63, C64, C66, C67, C69, C70, C71, C72, C73, C74, C82, C83, C84, C85, C86, C87, C88: 0.1uF; C0402
C11, C16, C24, C34, C60: 100UF; CAPAE660X800N
C12, C18, C21, C25, C26, C33, C36, C37, C45, C46, C62, C65, C68, C75, C76, C77, C78, C79: 4.7uF; C0402
C47, C48, C52, C53, C80, C81: 10uF; C1206
C49, C50, C54, C55: 10nF; C0402
C51, C56: 1nF; C0402
C57, C58, C59: 4.7nF; C0402
D1, D2, D3, D4, D5, D6: MBRA340T3; SMA
F1: FUSE; 3557
FAN0: blue; CHIP-LED0603
IC1, IC2, IC5, IC12, IC15: TMC2100-LA; QFN36-PAD
IC3, IC4, IC6, IC7, IC8, IC9, IC10, IC11, IC13, IC14, IC16, IC17, IC18, IC19: 74AHC1G126DCK; SC70-5
JP1, JP2: FIDUCIAL1X2.5; FIDUCIAL-1X2.5
L1, L2: 33uH; NR8040T330
LED1, LED2, LED3, LED4, LED5, LED6, LED7, LED8: blue; CHIP-LED0603
LOGO1: OSHW_LOGO_FILLX0200-NT; OSHW_FILLX200_NOTEXT
P8, P9: F-2X23-; DIL-100-2X23
Q1, Q2, Q3: AON6758; 8-DFN-EP-(5X6)
Q4, Q5, Q6, Q7: NPN-TRANSISTOR_SOT23; SOT23
R1, R2, R3, R4, R7, R8, R9, R10, R29, R30: 0.1R; R0805
R5, R11, R14, R15, R16, R19, R20, R21, R23, R24, R25, R28, R32, R33, R34, R36, R45, R46, R47, R48, R51, R54, R55, R56, R57, R61, R62, R63, R64, R65, R66: 4.7K; R0402
R6, R22, R27, R31, R35, R37, R38, R39, R40, R41, R43, R49, R50, R58, R60: 10K; R0402
R12: 44.3K; R0402
R13, R17, R18: 4K7, 1%; R0402
R26, R44: 39K; R0402
R42: 120K; R0402
R52, R53, R59, R70, R71: 2.2R; R0402
U1, U2, U3, U4, U5: SN74AHC595PW; SOP65P640X120-16N
U6, U10: RT8268; MSOP10
U11: PCA9685PW; SOP65P640X110-28N
U18: CAT24C256; SOIC127P600X175-8N
U19: CD4050BD; SOIC127P600X175-16N
U$4: CC-BY-SA
X1, X10, X13, X19, X22, X23: 22-05-7038-03; 7395-03
X2, X20: MSTBA4
X3, X21: MSTBA2
X4, X5, X6, X7, X8, X9, X11: 22-05-7028-02; 7395-02
X12, X14, X15, X16, X17, X18: 22-05-7048-04; 7395-04

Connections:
+3V3: 3.3V.TP, C2.1, C5.1, C13.1, C14.1, C15.1, C23.1, C30.1, C41.1, C42.1, C44.1, C61.1, C63.1, C84.1, C85.1, C86.1, C87.1, C88.1, IC1.8 (VCC_IO), IC2.8 (VCC_IO), IC3.5 (VCC), IC4.5 (VCC), IC5.8 (VCC_IO), IC8.5 (VCC), IC9.5 (VCC), IC10.5 (VCC), IC11.5 (VCC), IC12.8 (VCC_IO), IC13.5 (VCC), IC14.5 (VCC), IC15.8 (VCC_IO), IC16.5 (VCC), IC17.5 (VCC), IC18.5 (VCC), IC19.5 (VCC), P9.3, P9.4, R23.2, R24.2, R28.2, R36.2, R51.2, R54.2, U1.10 (~SRCLR), U1.16 (VCC), U2.10 (~SRCLR), U2.16 (VCC), U3.10 (~SRCLR), U3.16 (VCC), U4.10 (~SRCLR), U4.16 (VCC), U5.10 (~SRCLR), U5.16 (VCC), U18.3 (A2), U18.8 (VCC), U19.1 (VCC), X23.1
DALLAS_W1: P9.22, X23.2
DIR_E: IC12.7 (REFR_DIR), P8.15
DIR_H: IC15.7 (REFR_DIR), P8.16
DIR_X: IC1.7 (REFR_DIR), P8.26
DIR_Y: IC2.7 (REFR_DIR), P8.19
DIR_Z: IC5.7 (REFR_DIR), P8.14
ENABLE: P9.41, R23.1, U11.23 (~OE)
ENABLE_EH: IC12.22 (DRV_ENN_CFG6), IC15.22 (DRV_ENN_CFG6), IC19.4 (O)
ENABLE_XYZ: IC1.22 (DRV_ENN_CFG6), IC2.22 (DRV_ENN_CFG6), IC5.22 (DRV_ENN_CFG6), IC18.4 (O)
END_STOP_X_1: P9.25, U19.2 (G=A)
END_STOP_X_1_IN: R61.1, U19.3 (A), X22.1
END_STOP_X_2: P9.11, U19.10 (J=D)
END_STOP_X_2_IN: IC6.4 (O), R64.1, U19.9 (D), X10.1
END_STOP_Y_1: P9.23, U19.4 (H=B)
END_STOP_Y_1_IN: R62.1, U19.5 (B), X1.1
END_STOP_Y_2: P9.28, U19.12 (K=E)
END_STOP_Y_2_IN: IC7.4 (O), R65.1, U19.11 (E), X19.1
END_STOP_Z_1: P9.13, U19.6 (I=C)
END_STOP_Z_1_IN: R63.1, U19.7 (C), X13.1
END_STOP_Z_2: P9.18, U19.15 (L=F)
END_STOP_Z_2_IN: R66.1, U19.14 (F), X12.1
FAN0: Q6.1 (B), R34.2, U11.13 (LED7)
FAN1: Q7.1 (B), R33.2, U11.15 (LED8)
FAN2: Q4.1 (B), R32.2, U11.16 (LED9)
FAN3: Q5.1 (B), R5.2, U11.17 (LED10)
FAULT_E: IC12.20 (SWN_DIAG0), P8.18, R36.1
FAULT_H: IC15.20 (SWN_DIAG0), P8.8, R51.1
FAULT_X: IC1.20 (SWN_DIAG0), P8.10, R54.1
FAULT_Y: IC2.20 (SWN_DIAG0), P8.9, R24.1
FAULT_Z: IC5.20 (SWN_DIAG0), P9.24, R28.1
GND: C2.2, C4.2, C5.2, C6.2, C8.2, C10.2, C11.2, C12.2, C13.2, C14.2, C15.2, C16.2, C17.2, C18.2, C19.2, C20.1, C21.1, C23.2, C24.2, C25.2, C26.2, C27.2, C28.1, C29.2, C30.2, C31.2, C32.1, C33.1, C34.2, C36.2, C37.1, C40.2, C41.2, C42.2, C43.2, C44.2, C45.2, C46.2, C47.2, C48.2, C49.2, C52.2, C53.2, C54.2, C57.2, C58.2, C59.2, C60.2, C61.2, C62.2, C63.2, C64.1, C65.1, C67.1, C68.1, C70.2, C71.2, C72.2, C73.2, C74.2, C75.2, C76.2, C77.2, C78.2, C79.2, C80.2, C81.2, C82.2, C83.2, C84.2, C85.2, C86.2, C87.2, C88.2, D4.A, D5.A, D6.A, IC1.1 (CLK), IC1.10 (SPI_MODE), IC1.11 (GND), IC1.12 (GND), IC1.24 (GNDA), IC1.35 (GND), IC1.36 (TST_MODE), IC1.TP (GND), IC2.1 (CLK), IC2.10 (SPI_MODE), IC2.11 (GND), IC2.12 (GND), IC2.24 (GNDA), IC2.35 (GND), IC2.36 (TST_MODE), IC2.TP (GND), IC3.3 (GND), IC4.3 (GND), IC5.1 (CLK), IC5.10 (SPI_MODE), IC5.11 (GND), IC5.12 (GND), IC5.24 (GNDA), IC5.35 (GND), IC5.36 (TST_MODE), IC5.TP (GND), IC6.3 (GND), IC7.3 (GND), IC8.3 (GND), IC9.3 (GND), IC10.3 (GND), IC11.3 (GND), IC12.1 (CLK), IC12.10 (SPI_MODE), IC12.11 (GND), IC12.12 (GND), IC12.24 (GNDA), IC12.35 (GND), IC12.36 (TST_MODE), IC12.TP (GND), IC13.3 (GND), IC14.3 (GND), IC15.1 (CLK), IC15.10 (SPI_MODE), IC15.11 (GND), IC15.12 (GND), IC15.24 (GNDA), IC15.35 (GND), IC15.36 (TST_MODE), IC15.TP (GND), IC16.3 (GND), IC17.3 (GND), IC18.3 (GND), IC19.3 (GND), LED4.C, P8.1, P8.2, P9.1, P9.2, P9.43, P9.44, P9.45, P9.46, Q1.1 (S), Q1.2 (S), Q1.3 (S), Q2.1 (S), Q2.2 (S), Q2.3 (S), Q3.1 (S), Q3.2 (S), Q3.3 (S), Q4.2 (E), Q5.2 (E), Q6.2 (E), Q7.2 (E), R1.1, R2.1, R3.1, R4.1, R5.1, R7.1, R8.1, R9.1, R10.1, R22.2, R26.2, R29.1, R30.1, R32.1, R33.1, R34.1, R43.2, R44.2, R46.1, R47.1, R48.1, U1.8 (GND), U1.13 (~OE), U2.8 (GND), U2.13 (~OE), U3.8 (GND), U3.13 (~OE), U4.8 (GND), U4.13 (~OE), U5.8 (GND), U5.13 (~OE), U6.6 (GND), U6.EP, U10.6 (GND), U10.EP, U11.14 (VSS), U18.1 (A0), U18.2 (A1), U18.4 (GND), U19.8 (VSS), X1.2, X2.1, X2.2, X7.1, X8.1, X10.2, X11.1, X12.2, X13.2, X19.2, X22.2, X23.3
HEATER_E: Q3.4 (G), R47.2, U11.11 (LED5)
HEATER_H: Q2.4 (G), R48.2, U11.9 (LED3)
HEATER_HBP: Q1.4 (G), R46.2, U11.10 (LED4)
I2C2_SCL: P9.19, U11.26 (SCL), U18.6 (SCL)
I2C2_SDA: P9.20, U11.27 (SDA), U18.5 (SDA)
IREF_E: C79.1, R35.2, R60.1
IREF_E_RAW: R60.2, U11.21 (LED14)
IREF_H: C75.1, R31.1, R50.2
IREF_H_RAW: R31.2, U11.22 (LED15)
IREF_X: C77.1, R41.1, R49.2
IREF_X_RAW: R41.2, U11.18 (LED11)
IREF_Y: C76.1, R6.2, R37.1
IREF_Y_RAW: R37.2, U11.19 (LED12)
IREF_Z: C78.1, R27.2, R58.1
IREF_Z_RAW: R58.2, U11.20 (LED13)
unnamed: IC2.13 (OB1), X15.3
unnamed: C3.2, IC2.27 (CPO)
unnamed: IC4.1 (OE), U1.7 (QH)
unnamed: IC4.2 (I), U1.6 (QG)
unnamed: IC1.18 (ENCB_DCEN_CFG4), U1.2 (QC)
unnamed: LED8.C, R45.2
unnamed: LED5.A, R19.1
unnamed: FAN0.C, Q6.3 (C), X9.2
unnamed: C9.2, IC15.27 (CPO)
unnamed: IC15.14 (BRB), R9.2
unnamed: C7.2, IC5.27 (CPO)
unnamed: IC5.14 (BRB), R7.2
unnamed: C1.1, IC1.28 (CPI)
unnamed: C1.2, IC1.27 (CPO)
unnamed: IC1.14 (BRB), R1.2
unnamed: IC1.33 (BRA), R2.2
unnamed: C12.1, IC1.23 (AIN_IREF), R49.1
unnamed: FAN0.A, R25.1
unnamed: IC2.32 (OA2), X15.1
unnamed: R12.2, R22.1, U6.7 (FB)
unnamed: IC5.33 (BRA), R8.2
unnamed: C50.2, D6.C, L1.P$2, U6.5 (SW)
unnamed: C25.1, IC5.23 (AIN_IREF), R27.1
unnamed: C7.1, IC5.28 (CPI)
unnamed: IC5.3 (SCK_CFG2), IC10.4 (O)
unnamed: IC5.15 (OB2), X16.4
unnamed: IC15.33 (BRA), R10.2
unnamed: C21.2, IC1.25 (5VOUT), R53.1
unnamed: IC5.32 (OA2), X16.1
unnamed: C22.1, IC1.29 (VCP)
unnamed: IC3.2 (I), U1.4 (QE)
unnamed: IC2.14 (BRB), R3.2
unnamed: IC2.33 (BRA), R4.2
unnamed: IC5.13 (OB1), X16.3
unnamed: C18.1, IC2.23 (AIN_IREF), R6.1
unnamed: IC12.13 (OB1), X17.3
unnamed: IC3.1 (OE), U1.5 (QF)
unnamed: C3.1, IC2.28 (CPI)
unnamed: IC2.3 (SCK_CFG2), IC8.4 (O)
unnamed: IC1.19 (ENCA_DCIN_CFG5), U1.1 (QB)
unnamed: IC1.5 (SDO_NAO_CFG0), U1.3 (QD)
unnamed: IC2.15 (OB2), X15.4
unnamed: IC2.34 (OA1), X15.2
unnamed: C33.2, IC2.25 (5VOUT), R59.1
unnamed: C35.1, IC2.29 (VCP)
unnamed: IC2.4 (SDI_NAI_CFG1), IC9.4 (O)
unnamed: IC5.34 (OA1), X16.2
unnamed: C37.2, IC5.25 (5VOUT), R70.1
unnamed: C38.1, IC5.29 (VCP)
unnamed: IC2.5 (SDO_NAO_CFG0), U2.3 (QD)
unnamed: IC5.4 (SDI_NAI_CFG1), IC11.4 (O)
unnamed: IC5.5 (SDO_NAO_CFG0), U3.3 (QD)
unnamed: IC2.18 (ENCB_DCEN_CFG4), U2.2 (QC)
unnamed: IC5.18 (ENCB_DCEN_CFG4), U3.2 (QC)
unnamed: IC5.19 (ENCA_DCIN_CFG5), U3.1 (QB)
unnamed: IC11.1 (OE), U3.7 (QH)
unnamed: C49.1, U6.10 (SS)
unnamed: IC11.2 (I), U3.6 (QG)
unnamed: IC10.1 (OE), U3.5 (QF)
unnamed: IC10.2 (I), U3.4 (QE)
unnamed: C57.1, D3.A, LED1.C, Q2.5 (D), Q2.6 (D), Q2.7 (D), Q2.8 (D), Q2.TH (D), R57.1, X21.2
unnamed: IC2.19 (ENCA_DCIN_CFG5), U2.1 (QB)
unnamed: IC9.1 (OE), U2.7 (QH)
unnamed: IC9.2 (I), U2.6 (QG)
unnamed: IC8.1 (OE), U2.5 (QF)
unnamed: IC8.2 (I), U2.4 (QE)
unnamed: C39.2, IC12.27 (CPO)
unnamed: IC12.14 (BRB), R29.2
unnamed: IC12.33 (BRA), R30.2
unnamed: C50.1, U6.2 (BOOT)
unnamed: C62.1, IC12.23 (AIN_IREF), R35.1
unnamed: C39.1, IC12.28 (CPI)
unnamed: IC12.3 (SCK_CFG2), IC13.4 (O)
unnamed: IC12.15 (OB2), X17.4
unnamed: IC12.34 (OA1), X17.2
unnamed: C65.2, IC12.25 (5VOUT), R71.1
unnamed: C66.1, IC12.29 (VCP)
unnamed: IC12.4 (SDI_NAI_CFG1), IC14.4 (O)
unnamed: IC12.5 (SDO_NAO_CFG0), U4.3 (QD)
unnamed: IC12.18 (ENCB_DCEN_CFG4), U4.2 (QC)
unnamed: IC12.19 (ENCA_DCIN_CFG5), U4.1 (QB)
unnamed: IC14.1 (OE), U4.7 (QH)
unnamed: IC14.2 (I), U4.6 (QG)
unnamed: IC13.1 (OE), U4.5 (QF)
unnamed: C51.1, U6.8 (COMP)
unnamed: C36.1, IC15.23 (AIN_IREF), R50.1
unnamed: C9.1, IC15.28 (CPI)
unnamed: IC15.3 (SCK_CFG2), IC16.4 (O)
unnamed: IC15.15 (OB2), X18.4
unnamed: IC13.2 (I), U4.4 (QE)
unnamed: IC15.34 (OA1), X18.2
unnamed: C68.2, IC15.25 (5VOUT), R52.1
unnamed: LED4.A, R11.1
unnamed: C51.2, R26.1
unnamed: C69.1, IC15.29 (VCP)
unnamed: IC15.4 (SDI_NAI_CFG1), IC17.4 (O)
unnamed: IC15.5 (SDO_NAO_CFG0), U5.3 (QD)
unnamed: IC15.18 (ENCB_DCEN_CFG4), U5.2 (QC)
unnamed: IC15.19 (ENCA_DCIN_CFG5), U5.1 (QB)
unnamed: IC17.1 (OE), U5.7 (QH)
unnamed: IC17.2 (I), U5.6 (QG)
unnamed: IC16.1 (OE), U5.5 (QF)
unnamed: IC16.2 (I), U5.4 (QE)
unnamed: C70.1, IC15.26 (VCC), R52.2
unnamed: C71.1, IC1.26 (VCC), R53.2
unnamed: C73.1, IC5.26 (VCC), R70.2
unnamed: C72.1, IC2.26 (VCC), R59.2
unnamed: C74.1, IC12.26 (VCC), R71.2
unnamed: IC12.32 (OA2), X17.1
unnamed: IC15.13 (OB1), X18.3
unnamed: LED7.C, Q5.3 (C), X6.2
unnamed: LED6.C, Q4.3 (C), X5.2
unnamed: LED5.C, Q7.3 (C), X4.2
unnamed: LED6.A, R20.1
unnamed: LED7.A, R21.1
unnamed: IC15.32 (OA2), X18.1
unnamed: IC18.2 (I), U1.15 (QA)
unnamed: IC19.2 (I), U4.15 (QA)
unnamed: LED3.A, R15.1
unnamed: LED1.A, R14.1
unnamed: LED2.A, R16.1
unnamed: R42.2, R43.1, U10.7 (FB)
unnamed: C59.1, D1.A, LED3.C, Q3.5 (D), Q3.6 (D), Q3.7 (D), Q3.8 (D), Q3.TH (D), R55.1, X3.2
unnamed: R13.1, R38.1, X8.2
unnamed: C55.2, D4.C, L2.P$2, U10.5 (SW)
unnamed: R18.1, R40.1, X11.2
unnamed: R17.1, R39.1, X7.2
unnamed: C58.1, D2.A, LED2.C, Q1.5 (D), Q1.6 (D), Q1.7 (D), Q1.8 (D), Q1.TH (D), R56.1, X20.3, X20.4
unnamed: C54.1, U10.10 (SS)
unnamed: C56.1, U10.8 (COMP)
unnamed: C55.1, U10.2 (BOOT)
unnamed: C56.2, R44.1
SERVO_0: IC6.2 (I), P9.14
SERVO_0_EN: IC6.1 (OE), U2.15 (QA)
SERVO_1: IC7.2 (I), P9.16
SERVO_1_EN: IC7.1 (OE), U3.15 (QA)
SER_2: U1.9 (QH_2), U2.14 (SER)
SER_3: U2.9 (QH_2), U3.14 (SER)
SER_4: U3.9 (QH_2), U4.14 (SER)
SER_5: U4.9 (QH_2), U5.14 (SER)
SPI1_CS1: P9.42, U1.12 (RCLK), U2.12 (RCLK), U3.12 (RCLK), U4.12 (RCLK), U5.12 (RCLK)
SPI1_MOSI: P9.30, U1.14 (SER)
SPI1_SCLK: P9.31, U1.11 (SRCLK), U2.11 (SRCLK), U3.11 (SRCLK), U4.11 (SRCLK), U5.11 (SRCLK)
STEP_E: IC12.6 (REFL_STEP), P9.12
STEP_H: IC15.6 (REFL_STEP), P8.11
STEP_X: IC1.6 (REFL_STEP), P8.17
STEP_Y: IC2.6 (REFL_STEP), P8.12
STEP_Z: IC5.6 (REFL_STEP), P8.13
TERM_EXT1: C26.1, P9.33, R38.2
TERM_EXT2: C46.1, P9.36, R40.2
TERM_HBP: C45.1, P9.35, R39.2
TRISTATE_STEPPERS: IC18.1 (OE), IC19.1 (OE), U5.15 (QA)
VDD_5V: 5V.TP, C17.1, C48.1, C80.1, C82.1, C83.1, IC6.5 (VCC), IC7.5 (VCC), L1.P$1, P9.5, P9.6, R12.1, R61.2, R62.2, R63.2, R64.2, R65.2, R66.2, U11.1 (A0), U11.2 (A1), U11.3 (A2), U11.4 (A3), U11.5 (A4), U11.24 (A5), U11.28 (VDD), X1.3, X10.3, X12.3, X13.3, X19.3, X22.3
VDD_12V: 12V.TP, C53.1, C81.1, L2.P$1, R11.2, R19.2, R20.2, R21.2, R25.2, R42.1, X4.1, X5.1, X6.1, X9.1, X12.4
VDD_ADC: P9.32, R13.2, R17.2, R18.2
VDD_IN: 12..24V.TP, C4.1, C6.1, C8.1, C10.1, C11.1, C16.1, C19.1, C20.2, C22.2, C24.1, C27.1, C28.2, C29.1, C31.1, C32.2, C34.1, C35.2, C38.2, C40.1, C43.1, C47.1, C52.1, C60.1, C64.2, C66.2, C67.2, C69.2, D1.C, D2.C, D3.C, D5.C, F1.P$3 (2), F1.P$4 (2), IC1.16 (VS), IC1.30 (VSA), IC1.31 (VS), IC2.16 (VS), IC2.30 (VSA), IC2.31 (VS), IC5.16 (VS), IC5.30 (VSA), IC5.31 (VS), IC12.16 (VS), IC12.30 (VSA), IC12.31 (VS), IC15.16 (VS), IC15.30 (VSA), IC15.31 (VS), R14.2, R15.2, R16.2, R45.1, R55.2, R56.2, R57.2, U6.4 (VIN), U10.4 (VIN), X3.1, X20.1, X20.2, X21.1
VIN: F1.P$1 (1), F1.P$2 (1), LED8.A, X2.3, X2.4
X_A1: IC1.34 (OA1), X14.2
X_A2: IC1.32 (OA2), X14.1
X_B1: IC1.13 (OB1), X14.3
X_B2: IC1.15 (OB2), X14.4
X_CFG1: IC1.4 (SDI_NAI_CFG1), IC4.4 (O)
X_CFG2: IC1.3 (SCK_CFG2), IC3.4 (O)

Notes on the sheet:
Fan drivers
PWM extension
Power in
5V step down converter
12V step down converter
MOSFET E
MOSFET HBP
MOSFET H
End stops 2
Thermistors
End stops 1
EEPROM
Dallas 1W

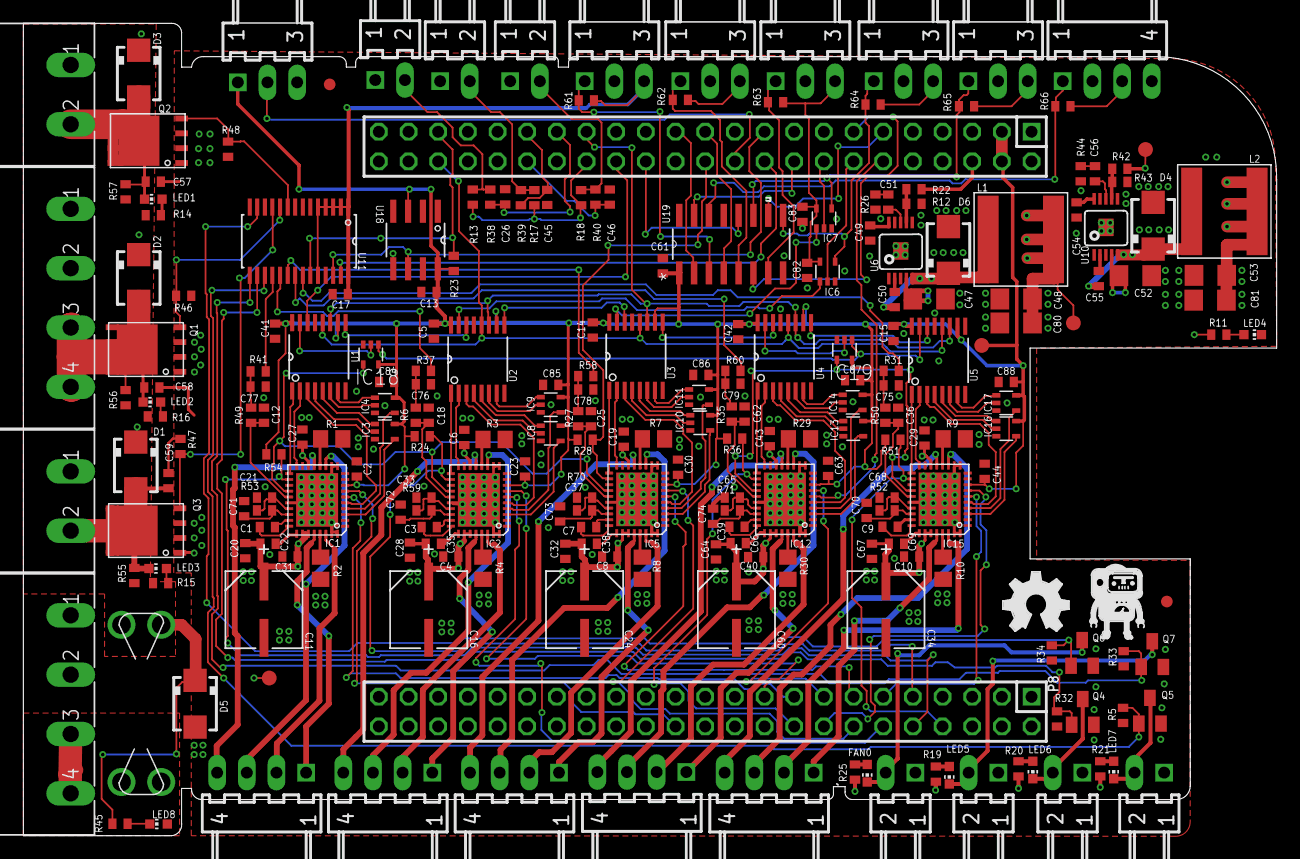
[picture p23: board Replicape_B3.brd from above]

Board: 4 copper layers, 107.3 x 69.5 mm, 244 parts (0 on the bottom side), 210 nets.

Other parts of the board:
U$1: LOGO_BIG

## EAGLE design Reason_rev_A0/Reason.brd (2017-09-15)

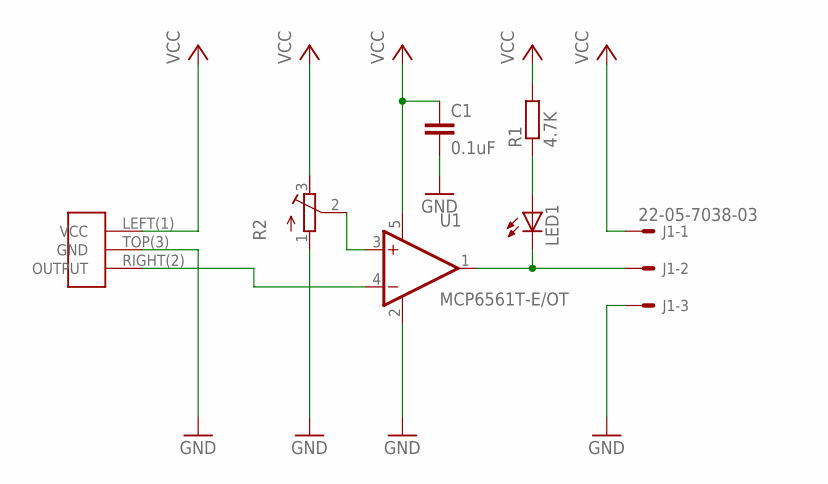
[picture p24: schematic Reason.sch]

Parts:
C1: 0.1uF; C0402
J1: 22-05-7038-03; 7395-03
LED1: LEDCHIPLED_0603; CHIPLED_0603
R1: 4.7K; R0402
R2: R-TRIMM5W; RTRIM5W
U1: MCP6561T-E/OT; SOT95P270X145-5N
U2: SS39ET; SOT-23

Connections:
GND: C1.2, J1.3, R2.1 (E), U1.2 (VSS), U2.TOP(3) (GND)
unnamed: J1.2, LED1.C, U1.1 (VOUT)
unnamed: LED1.A, R1.1
unnamed: R2.2 (S), U1.3 (VIN+)
unnamed: U1.4 (VIN-), U2.RIGHT(2) (OUTPUT)
VCC: C1.1, J1.1, R1.2, R2.3 (A), U1.5 (VDD), U2.LEFT(1) (VCC)

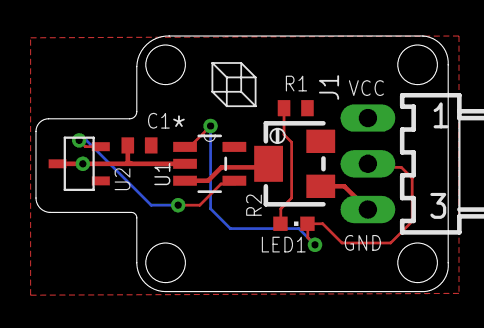
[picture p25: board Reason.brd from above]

Board: 2 copper layers, 22.9 x 14.2 mm, 7 parts (0 on the bottom side), 6 nets.

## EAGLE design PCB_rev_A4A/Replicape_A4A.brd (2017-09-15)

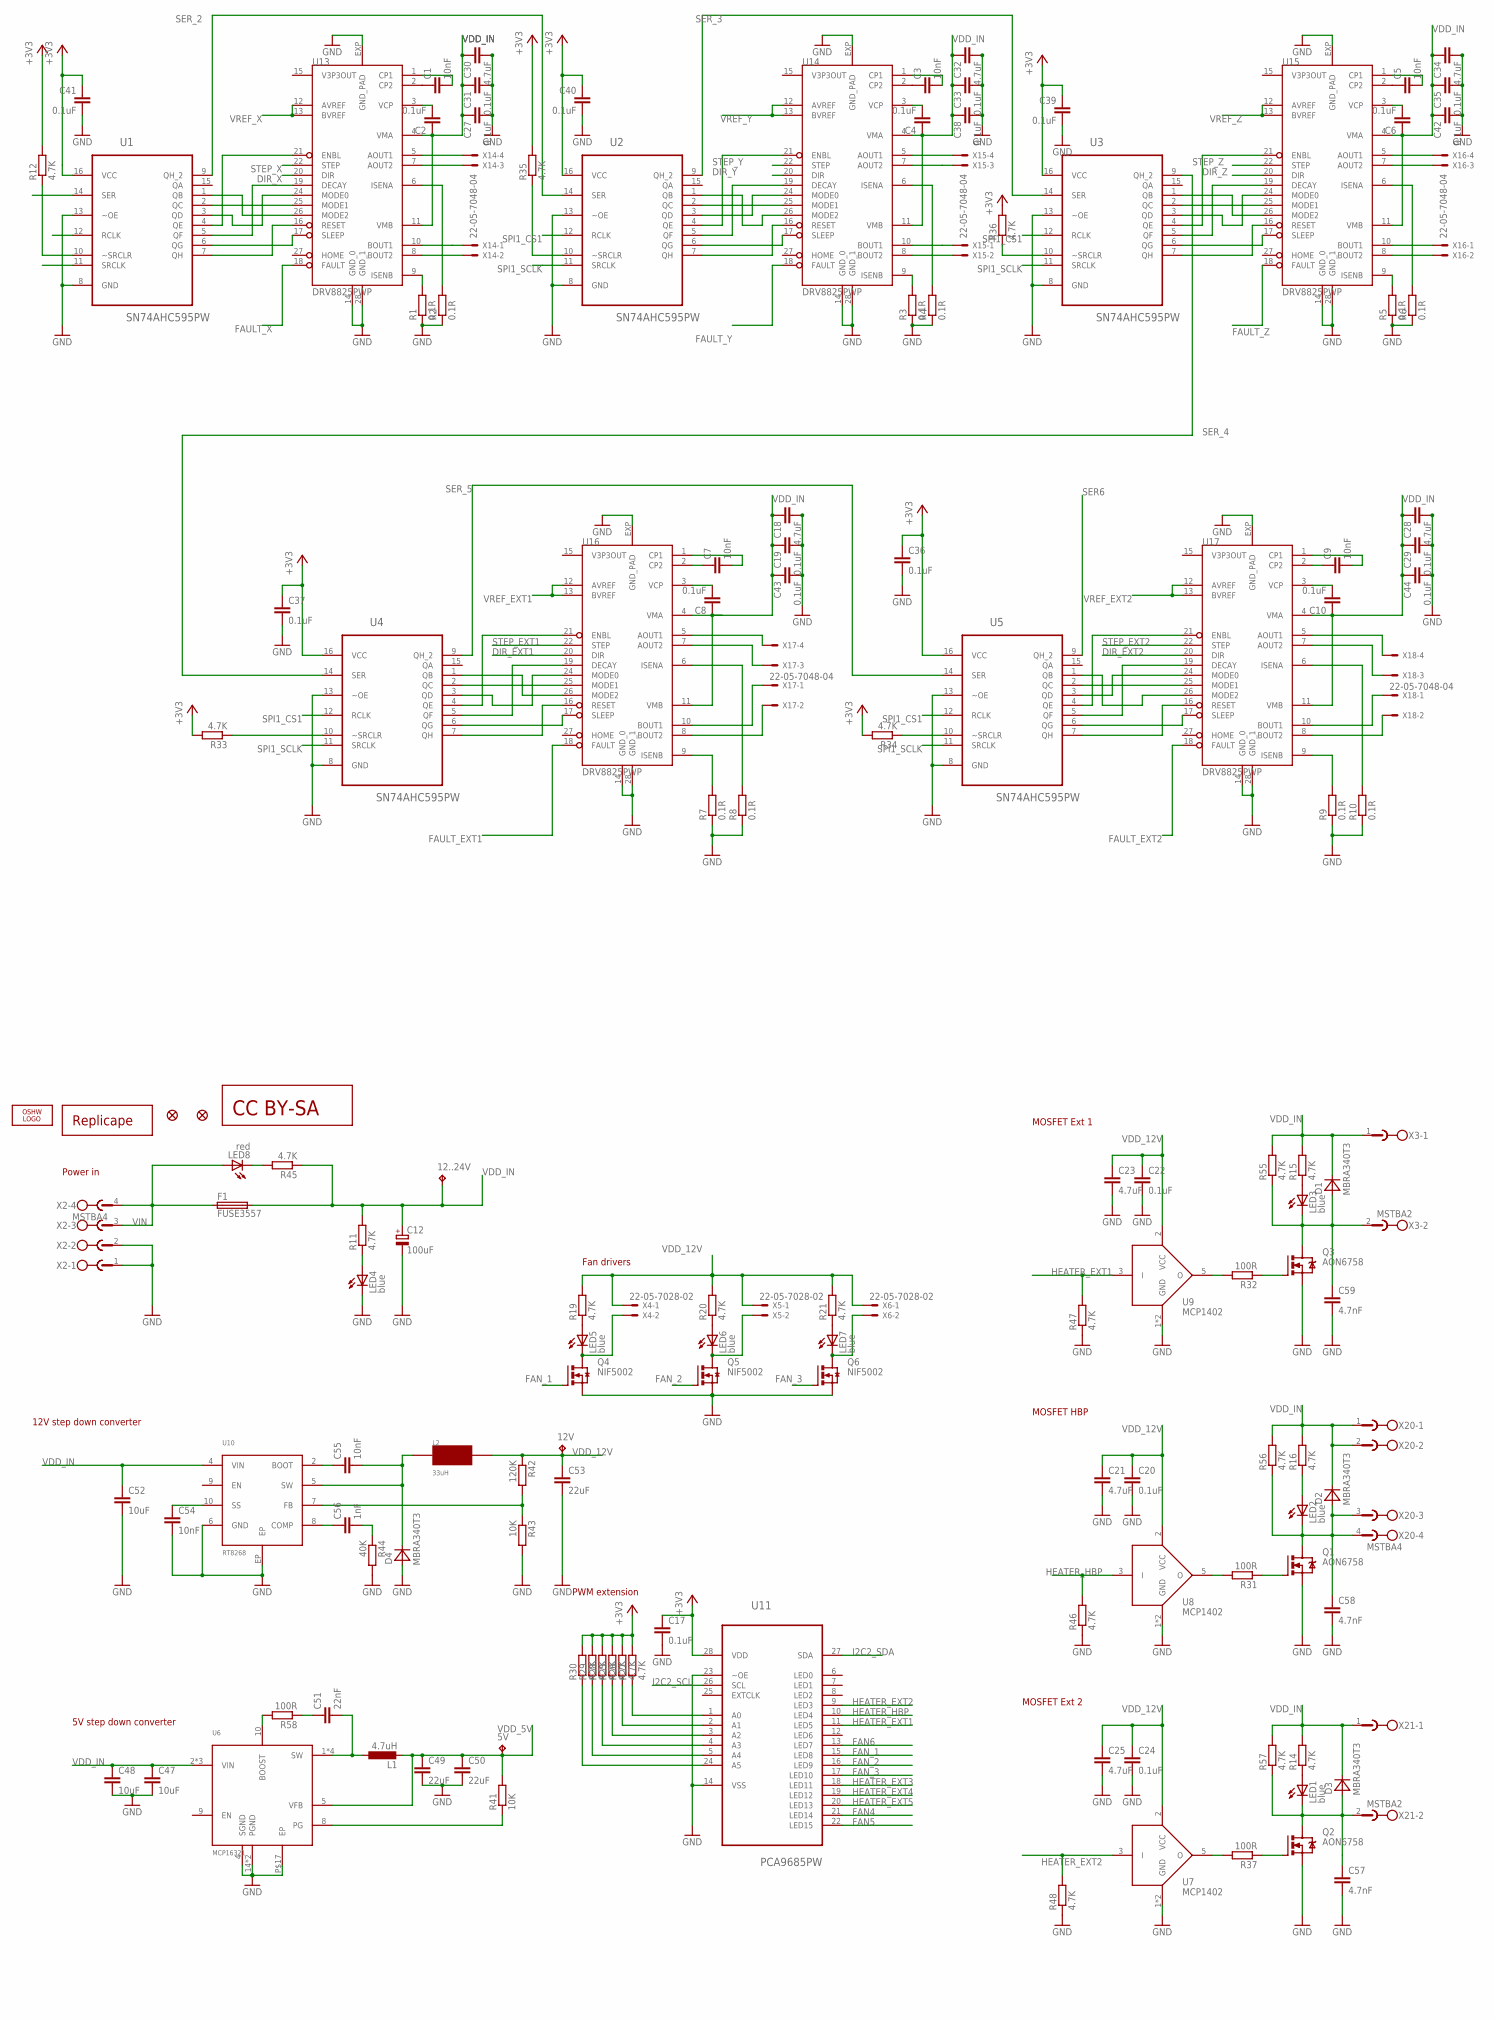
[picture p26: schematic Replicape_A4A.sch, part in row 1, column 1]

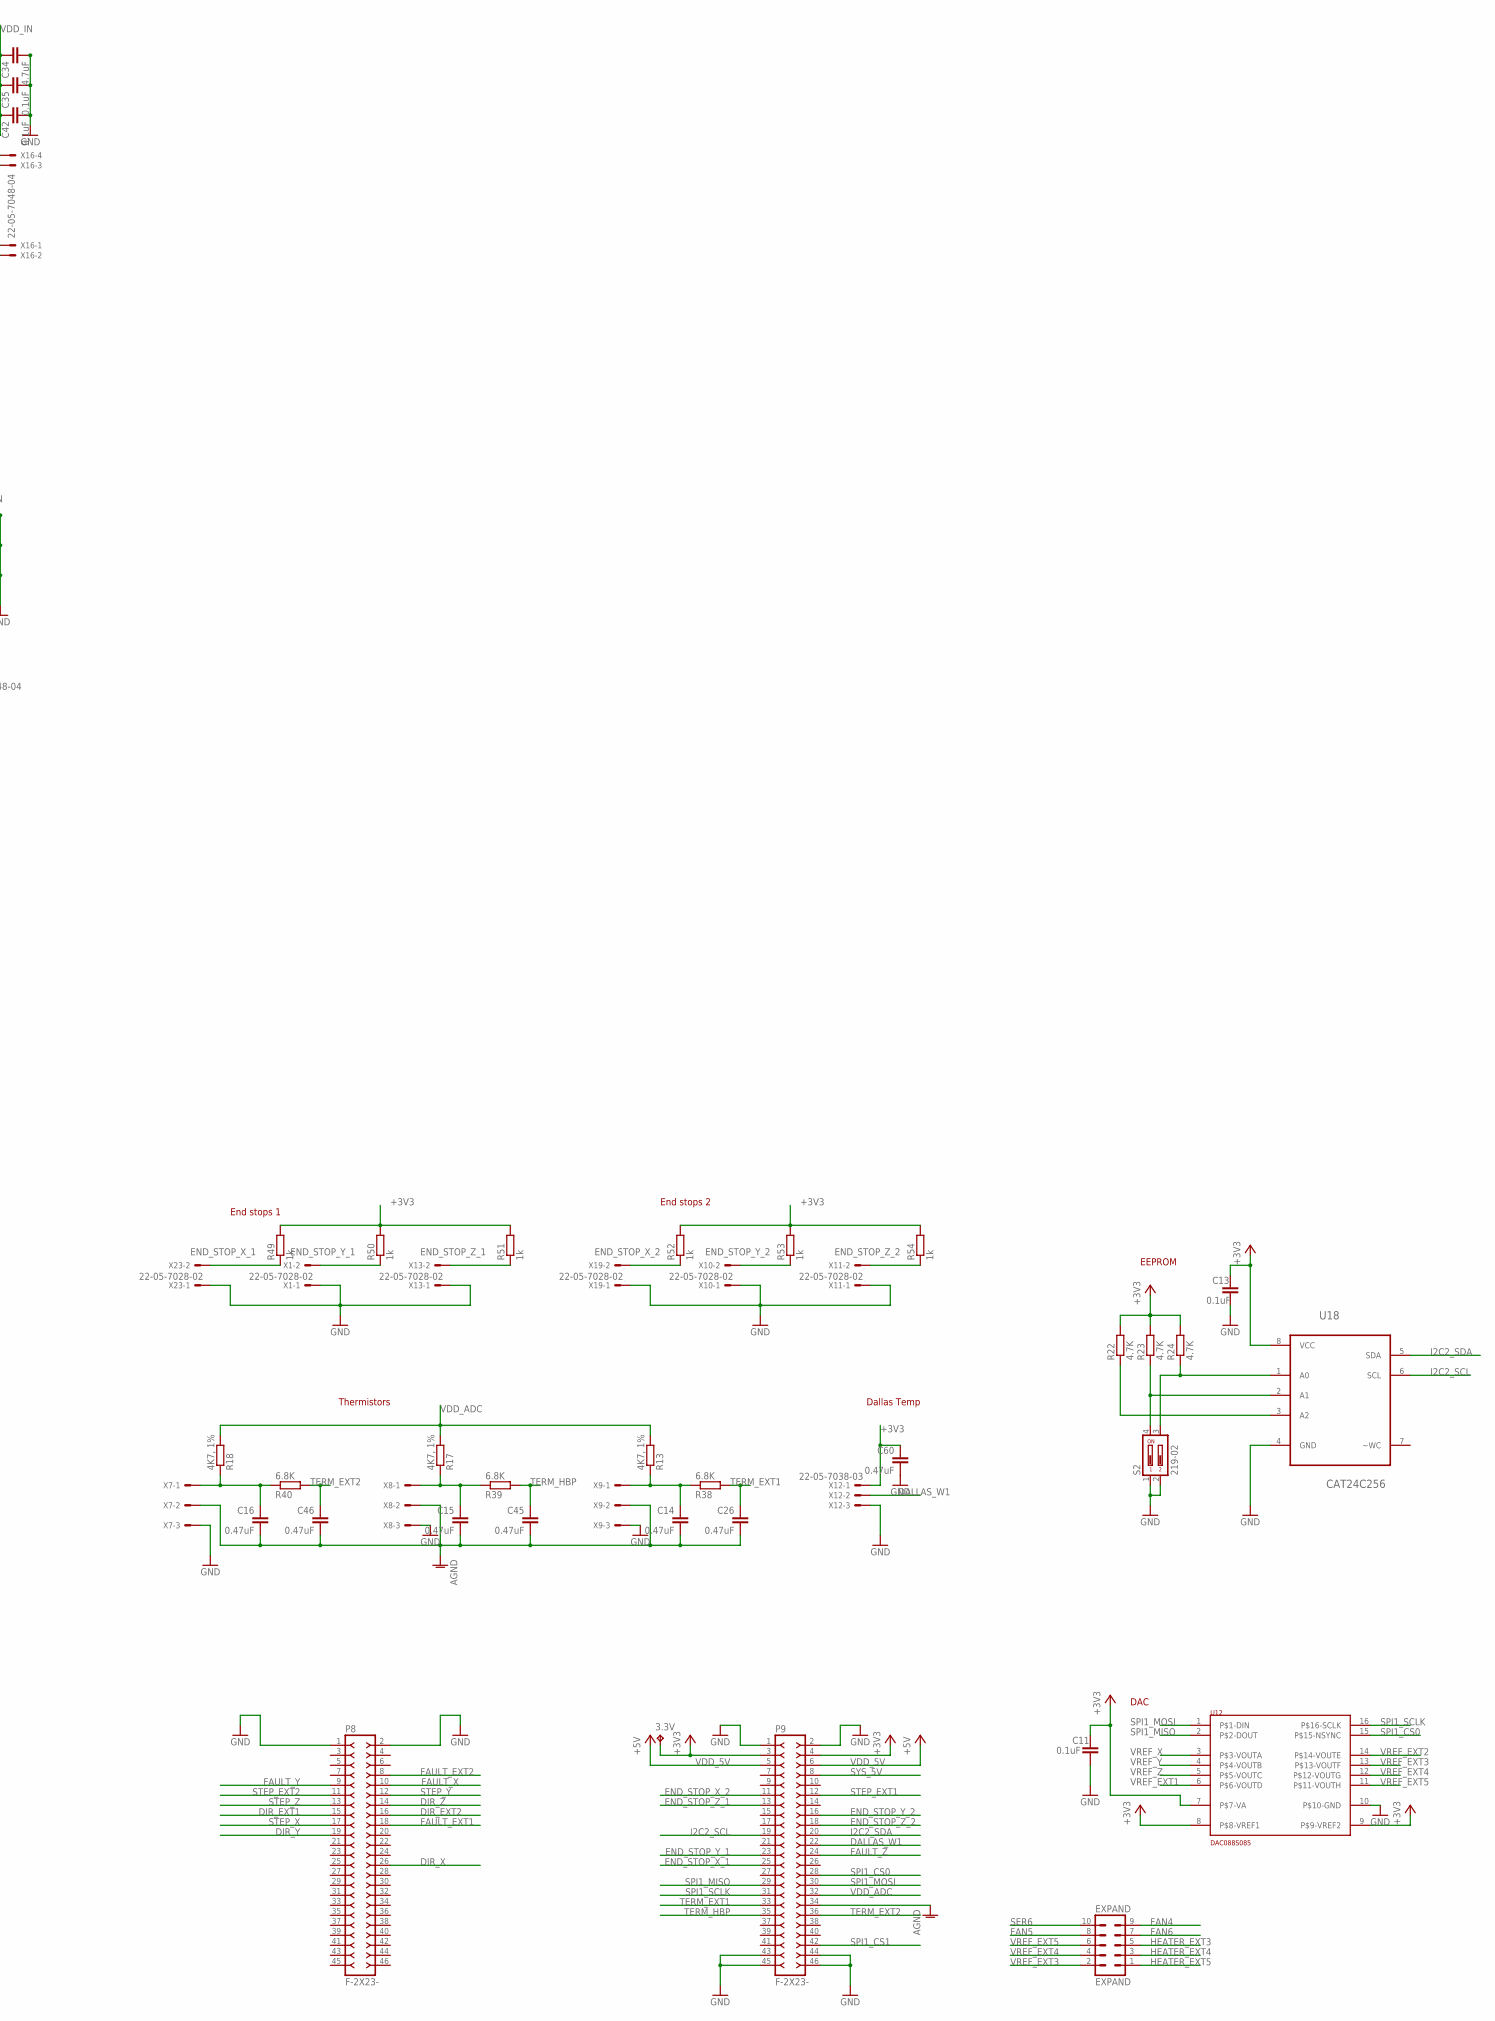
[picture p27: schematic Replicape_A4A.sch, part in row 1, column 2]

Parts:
3.3V, 5V, 12..24V, 12V: TPB1,27; B1,27
C1, C3, C5, C7, C9, C54, C55: 10nF; C0402
C2, C4, C6, C8, C10, C11, C13, C17, C19, C20, C22, C24, C27, C29, C31, C33, C35, C36, C37, C38, C39, C40, C41, C42, C43, C44: 0.1uF; C0402
C12: 100uF; 140CLH-0810
C14, C15, C16, C26, C45, C46, C60: 0.47uF; C0402
C18, C28, C30, C32, C34: 4.7uF; C0603
C21, C23, C25: 4.7uF; C0402
C47, C48, C52: 10uF; C1206
C49, C50, C53: 22uF; C0805
C51: 22nF; C0402
C56: 1nF; C0402
C57, C58, C59: 4.7nF; C0402
D1, D2, D3, D4: MBRA340T3; SMA
EXPAND: EXPAND; MA05-2
F1: FUSE3557; 3557
JP1, JP2: FIDUCIAL1X2.5; FIDUCIAL-1X2.5
L1: 4.7uH; VLC5020
L2: 33uH; NR8040T330
LED1, LED2, LED3, LED4, LED5, LED6, LED7: blue; CHIP-LED0603
LED8: red; CHIP-LED0603
LOGO1: OSHW_LOGO_FILLX0200-NT; OSHW_FILLX200_NOTEXT
P8, P9: F-2X23-; DIL-100-2X23
Q1, Q2, Q3: AON6758; 8-DFN-EP-(5X6)
Q4, Q5, Q6: NIF5002; SOT223
R1, R2, R3, R4, R5, R6, R7, R8, R9, R10: 0.1R; R0805
R11, R12, R14, R15, R16, R19, R20, R21, R22, R23, R24, R25, R26, R27, R28, R29, R30, R33, R34, R35, R36, R45, R46, R47, R48, R55, R56, R57: 4.7K; R0402
R13, R17, R18: 4K7, 1%; R0402
R31, R32, R37, R58: 100R; R0402
R38, R39, R40: 6.8K; R0402
R41, R43: 10K; R0402
R42: 120K; R0402
R44: 40K; R0402
R49, R50, R51, R52, R53, R54: 1k; R0402
S2: 219-02; CTS-219-02
U1, U2, U3, U4, U5: SN74AHC595PW; SOP65P640X120-16N
U6: MCP16321; QFN-16
U7, U8, U9: MCP1402; SOT23-5L
U10: RT8268; MSOP10
U11: PCA9685PW; SOP65P640X110-28N
U12: DAC088S085; TSSOP-16
U13, U14, U15, U16, U17: DRV8825PWP; TSSOP-28
U18: CAT24C256; SOIC127P600X175-8N
U$2: REPLICAPE-LOGO
U$3: CC-BY-SA
X1, X4, X5, X6, X10, X11, X13, X19, X23: 22-05-7028-02; 7395-02
X2, X20: MSTBA4
X3, X21: MSTBA2
X7, X8, X9, X12: 22-05-7038-03; 7395-03
X14, X15, X16, X17, X18: 22-05-7048-04; 7395-04

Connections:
+3V3: 3.3V.TP, C11.1, C13.1, C17.1, C36.1, C37.1, C39.1, C40.1, C41.1, C60.1, P9.3, P9.4, R12.2, R22.2, R23.2, R24.2, R25.2, R26.2, R27.2, R28.2, R29.2, R30.2, R33.2, R34.2, R35.2, R36.2, R49.2, R50.2, R51.2, R52.2, R53.2, R54.2, U1.16 (VCC), U2.16 (VCC), U3.16 (VCC), U4.16 (VCC), U5.16 (VCC), U11.28 (VDD), U12.7 (P$7-VA), U12.8 (P$8-VREF1), U12.9 (P$9-VREF2), U18.8 (VCC), X12.1
A1_X: U13.5 (AOUT1), X14.4
A2_X: U13.7 (AOUT2), X14.3
AGND: C14.2, C15.2, C16.2, C26.2, C45.2, C46.2, P9.34, X7.2, X8.2, X9.2
B1_X: U13.10 (BOUT1), X14.1
DALLAS_W1: P9.22, X12.2
DIR_EXT1: P8.15, U16.20 (DIR)
DIR_EXT2: P8.16, U17.20 (DIR)
DIR_X: P8.26, U13.20 (DIR)
DIR_Y: P8.19, U14.20 (DIR)
DIR_Z: P8.14, U15.20 (DIR)
END_STOP_X_1: P9.25, R49.1, X23.2
END_STOP_X_2: P9.11, R52.1, X19.2
END_STOP_Y_1: P9.23, R50.1, X1.2
END_STOP_Y_2: P9.16, R53.1, X10.2
END_STOP_Z_1: P9.13, R51.1, X13.2
END_STOP_Z_2: P9.18, R54.1, X11.2
EXT1_DECAY: U4.5 (QF), U16.19 (DECAY)
EXT1_MODE0: U4.3 (QD), U16.24 (MODE0)
EXT1_MODE1: U4.2 (QC), U16.25 (MODE1)
EXT1_MODE2: U4.1 (QB), U16.26 (MODE2)
EXT1_NENABLE: U4.4 (QE), U16.21 (ENBL)
EXT1_NRESET: U4.7 (QH), U16.16 (RESET)
EXT1_NSLEEP: U4.6 (QG), U16.17 (SLEEP)
EXT2_DECAY: U5.5 (QF), U17.19 (DECAY)
EXT2_MODE0: U5.3 (QD), U17.24 (MODE0)
EXT2_MODE1: U5.2 (QC), U17.25 (MODE1)
EXT2_MODE2: U5.1 (QB), U17.26 (MODE2)
EXT2_NENABLE: U5.4 (QE), U17.21 (ENBL)
EXT2_NRESET: U5.7 (QH), U17.16 (RESET)
EXT2_NSLEEP: U5.6 (QG), U17.17 (SLEEP)
FAN4: EXPAND.9, U11.21 (LED14)
FAN5: EXPAND.8, U11.22 (LED15)
FAN6: EXPAND.7, U11.13 (LED7)
FAN_1: Q4.1 (G), U11.15 (LED8)
FAN_2: Q5.1 (G), U11.16 (LED9)
FAN_3: Q6.1 (G), U11.17 (LED10)
FAULT_EXT1: P8.18, U16.18 (FAULT)
FAULT_EXT2: P8.8, U17.18 (FAULT)
FAULT_X: P8.10, U13.18 (FAULT)
FAULT_Y: P8.9, U14.18 (FAULT)
FAULT_Z: P9.24, U15.18 (FAULT)
GND: C11.2, C12.-, C13.2, C17.2, C18.2, C19.2, C20.2, C21.2, C22.2, C23.2, C24.2, C25.2, C27.2, C28.2, C29.2, C30.2, C31.2, C32.2, C33.2, C34.2, C35.2, C36.2, C37.2, C38.2, C39.2, C40.2, C41.2, C42.2, C43.2, C44.2, C47.2, C48.2, C49.2, C50.2, C52.2, C53.2, C54.2, C57.2, C58.2, C59.2, C60.2, D4.A, LED4.C, P8.1, P8.2, P9.1, P9.2, P9.43, P9.44, P9.45, P9.46, Q1.1 (S), Q1.2 (S), Q1.3 (S), Q2.1 (S), Q2.2 (S), Q2.3 (S), Q3.1 (S), Q3.2 (S), Q3.3 (S), Q4.3 (S), Q5.3 (S), Q6.3 (S), R1.1, R2.1, R3.1, R4.1, R5.1, R6.1, R7.1, R8.1, R9.1, R10.1, R43.2, R44.2, R46.1, R47.1, R48.1, S2.1, S2.2, U1.8 (GND), U1.13 (~OE), U2.8 (GND), U2.13 (~OE), U3.8 (GND), U3.13 (~OE), U4.8 (GND), U4.13 (~OE), U5.8 (GND), U5.13 (~OE), U6.4 (SGND), U6.14 (PGND), U6.15 (PGND), U6.P$17 (EP), U7.1 (GND), U7.4 (GND), U8.1 (GND), U8.4 (GND), U9.1 (GND), U9.4 (GND), U10.6 (GND), U10.EP, U11.14 (VSS), U11.23 (~OE), U12.10 (P$10-GND), U13.14 (GND_0), U13.28 (GND_1), U13.EXP (GND_PAD), U14.14 (GND_0), U14.28 (GND_1), U14.EXP (GND_PAD), U15.14 (GND_0), U15.28 (GND_1), U15.EXP (GND_PAD), U16.14 (GND_0), U16.28 (GND_1), U16.EXP (GND_PAD), U17.14 (GND_0), U17.28 (GND_1), U17.EXP (GND_PAD), U18.4 (GND), X1.1, X2.1, X2.2, X7.3, X8.3, X9.3, X10.1, X11.1, X12.3, X13.1, X19.1, X23.1
HEATER_EXT1: R47.2, U9.3 (I), U11.11 (LED5)
HEATER_EXT2: R48.2, U7.3 (I), U11.9 (LED3)
HEATER_EXT3: EXPAND.5, U11.18 (LED11)
HEATER_EXT4: EXPAND.3, U11.19 (LED12)
HEATER_EXT5: EXPAND.1, U11.20 (LED13)
HEATER_HBP: R46.2, U8.3 (I), U11.10 (LED4)
I2C2_SCL: P9.19, U11.26 (SCL), U18.6 (SCL)
I2C2_SDA: P9.20, U11.27 (SDA), U18.5 (SDA)
unnamed: C51.1, R58.1
unnamed: U13.8 (BOUT2), X14.2
unnamed: U14.8 (BOUT2), X15.2
unnamed: U15.10 (BOUT1), X16.1
unnamed: U15.8 (BOUT2), X16.2
unnamed: LED8.C, R45.2
unnamed: LED5.A, R19.1
unnamed: C1.1, U13.2 (CP2)
unnamed: C1.2, U13.1 (CP1)
unnamed: R1.2, U13.9 (ISENB)
unnamed: R2.2, U13.6 (ISENA)
unnamed: R32.2, U9.5 (O)
unnamed: C2.2, U13.3 (VCP)
unnamed: Q2.4 (G), R37.1
unnamed: C3.1, U14.2 (CP2)
unnamed: C3.2, U14.1 (CP1)
unnamed: R3.2, U14.9 (ISENB)
unnamed: R4.2, U14.6 (ISENA)
unnamed: C4.2, U14.3 (VCP)
unnamed: R37.2, U7.5 (O)
unnamed: C5.1, U15.2 (CP2)
unnamed: C5.2, U15.1 (CP1)
unnamed: R5.2, U15.9 (ISENB)
unnamed: R6.2, U15.6 (ISENA)
unnamed: C6.2, U15.3 (VCP)
unnamed: R27.1, U11.1 (A0)
unnamed: R26.1, U11.2 (A1)
unnamed: Q1.4 (G), R31.1
unnamed: R31.2, U8.5 (O)
unnamed: C57.1, D3.A, LED1.C, Q2.5 (D), Q2.6 (D), Q2.7 (D), Q2.8 (D), Q2.TH (D), R57.1, X21.2
unnamed: C7.1, U16.2 (CP2)
unnamed: C7.2, U16.1 (CP1)
unnamed: R7.2, U16.9 (ISENB)
unnamed: R8.2, U16.6 (ISENA)
unnamed: C8.2, U16.3 (VCP)
unnamed: R25.1, U11.3 (A2)
unnamed: C9.1, U17.2 (CP2)
unnamed: C9.2, U17.1 (CP1)
unnamed: R9.2, U17.9 (ISENB)
unnamed: R10.2, U17.6 (ISENA)
unnamed: C10.2, U17.3 (VCP)
unnamed: R28.1, U11.4 (A3)
unnamed: R29.1, U11.5 (A4)
unnamed: LED4.A, R11.1
unnamed: R12.1, U1.10 (~SRCLR)
unnamed: R33.1, U4.10 (~SRCLR)
unnamed: R34.1, U5.10 (~SRCLR)
unnamed: R35.1, U2.10 (~SRCLR)
unnamed: R36.1, U3.10 (~SRCLR)
unnamed: R30.1, U11.24 (A5)
unnamed: LED7.C, Q6.2 (D), Q6.4 (D), X6.2
unnamed: LED6.C, Q5.2 (D), Q5.4 (D), X5.2
unnamed: LED5.C, Q4.2 (D), Q4.4 (D), X4.2
unnamed: LED6.A, R20.1
unnamed: LED7.A, R21.1
unnamed: LED3.A, R15.1
unnamed: R58.2, U6.10 (BOOST)
unnamed: LED1.A, R14.1
unnamed: LED2.A, R16.1
unnamed: Q3.4 (G), R32.1
unnamed: R24.1, S2.3, U18.1 (A0)
unnamed: R23.1, S2.4, U18.2 (A1)
unnamed: R22.1, U18.3 (A2)
unnamed: R42.2, R43.1, U10.7 (FB)
unnamed: C59.1, D1.A, LED3.C, Q3.5 (D), Q3.6 (D), Q3.7 (D), Q3.8 (D), Q3.TH (D), R55.1, X3.2
unnamed: C14.1, R13.1, R38.1, X9.1
unnamed: C55.2, D4.C, L2.P$2, U10.5 (SW)
unnamed: R41.1, U6.8 (PG)
unnamed: C16.1, R18.1, R40.1, X7.1
unnamed: C15.1, R17.1, R39.1, X8.1
unnamed: C58.1, D2.A, LED2.C, Q1.5 (D), Q1.6 (D), Q1.7 (D), Q1.8 (D), Q1.TH (D), R56.1, X20.3, X20.4
unnamed: C54.1, U10.10 (SS)
unnamed: C56.1, U10.8 (COMP)
unnamed: C55.1, U10.2 (BOOT)
unnamed: C56.2, R44.1
SER6: EXPAND.10, U5.9 (QH_2)
SER_2: U1.9 (QH_2), U2.14 (SER)
SER_3: U2.9 (QH_2), U3.14 (SER)
SER_4: U3.9 (QH_2), U4.14 (SER)
SER_5: U4.9 (QH_2), U5.14 (SER)
SPI1_CS0: P9.28, U12.15 (P$15-NSYNC)
SPI1_CS1: P9.42, U1.12 (RCLK), U2.12 (RCLK), U3.12 (RCLK), U4.12 (RCLK), U5.12 (RCLK)
SPI1_MISO: P9.29, U12.2 (P$2-DOUT)
SPI1_MOSI: P9.30, U1.14 (SER), U12.1 (P$1-DIN)
SPI1_SCLK: P9.31, U1.11 (SRCLK), U2.11 (SRCLK), U3.11 (SRCLK), U4.11 (SRCLK), U5.11 (SRCLK), U12.16 (P$16-SCLK)
STEP1_EXT1: U16.5 (AOUT1), X17.4
STEP1_EXT2: U17.5 (AOUT1), X18.4
STEP1_Y: U14.5 (AOUT1), X15.4
STEP1_Z: U15.5 (AOUT1), X16.4
STEP2_EXT1: U16.7 (AOUT2), X17.3
STEP2_EXT2: U17.7 (AOUT2), X18.3
STEP2_Y: U14.7 (AOUT2), X15.3
STEP2_Z: U15.7 (AOUT2), X16.3
STEP3_EXT1: U16.10 (BOUT1), X17.1
STEP3_EXT2: U17.10 (BOUT1), X18.1
STEP3_Y: U14.10 (BOUT1), X15.1
STEP4_EXT1: U16.8 (BOUT2), X17.2
STEP4_EXT2: U17.8 (BOUT2), X18.2
STEP_EXT1: P9.12, U16.22 (STEP)
STEP_EXT2: P8.11, U17.22 (STEP)
STEP_X: P8.17, U13.22 (STEP)
STEP_Y: P8.12, U14.22 (STEP)
STEP_Z: P8.13, U15.22 (STEP)
SW: C51.2, L1.1, U6.1 (SW), U6.12 (SW), U6.13 (SW), U6.16 (SW)
SYS_5V: P9.8
TERM_EXT1: C26.1, P9.33, R38.2
TERM_EXT2: C46.1, P9.36, R40.2
TERM_HBP: C45.1, P9.35, R39.2
VDD_5V: 5V.TP, C49.1, C50.1, L1.2, P9.5, P9.6, R41.2, U6.5 (VFB)
VDD_12V: 12V.TP, C20.1, C21.1, C22.1, C23.1, C24.1, C25.1, C53.1, L2.P$1, R19.2, R20.2, R21.2, R42.1, U7.2 (VCC), U8.2 (VCC), U9.2 (VCC), X4.1, X5.1, X6.1
VDD_ADC: P9.32, R13.2, R17.2, R18.2
VDD_IN: 12..24V.TP, C2.1, C4.1, C6.1, C8.1, C10.1, C12.+, C18.1, C19.1, C27.1, C28.1, C29.1, C30.1, C31.1, C32.1, C33.1, C34.1, C35.1, C38.1, C42.1, C43.1, C44.1, C47.1, C48.1, C52.1, D1.C, D2.C, D3.C, F1.3 (2), F1.4 (2), R11.2, R14.2, R15.2, R16.2, R45.1, R55.2, R56.2, R57.2, U6.2 (VIN), U6.3 (VIN), U6.11 (VIN), U10.4 (VIN), U13.4 (VMA), U13.11 (VMB), U14.4 (VMA), U14.11 (VMB), U15.4 (VMA), U15.11 (VMB), U16.4 (VMA), U16.11 (VMB), U17.4 (VMA), U17.11 (VMB), X3.1, X20.1, X20.2, X21.1
VIN: F1.1, F1.2 (1), LED8.A, X2.3, X2.4
VREF_EXT1: U12.6 (P$6-VOUTD), U16.12 (AVREF), U16.13 (BVREF)
VREF_EXT2: U12.14 (P$14-VOUTE), U17.12 (AVREF), U17.13 (BVREF)
VREF_EXT3: EXPAND.2, U12.13 (P$13-VOUTF)
VREF_EXT4: EXPAND.4, U12.12 (P$12-VOUTG)
VREF_EXT5: EXPAND.6, U12.11 (P$11-VOUTH)
VREF_X: U12.3 (P$3-VOUTA), U13.12 (AVREF), U13.13 (BVREF)
VREF_Y: U12.4 (P$4-VOUTB), U14.12 (AVREF), U14.13 (BVREF)
VREF_Z: U12.5 (P$5-VOUTC), U15.12 (AVREF), U15.13 (BVREF)
X_DECAY: U1.5 (QF), U13.19 (DECAY)
X_MODE0: U1.3 (QD), U13.24 (MODE0)
X_MODE1: U1.2 (QC), U13.25 (MODE1)
X_MODE2: U1.1 (QB), U13.26 (MODE2)
X_NENABLE: U1.4 (QE), U13.21 (ENBL)
X_NRESET: U1.7 (QH), U13.16 (RESET)
X_NSLEEP: U1.6 (QG), U13.17 (SLEEP)
Y_DECAY: U2.5 (QF), U14.19 (DECAY)
Y_MODE0: U2.3 (QD), U14.24 (MODE0)
Y_MODE1: U2.2 (QC), U14.25 (MODE1)
Y_MODE2: U2.1 (QB), U14.26 (MODE2)
Y_NENABLE: U2.4 (QE), U14.21 (ENBL)
Y_NRESET: U2.7 (QH), U14.16 (RESET)
Y_NSLEEP: U2.6 (QG), U14.17 (SLEEP)
Z_DECAY: U3.5 (QF), U15.19 (DECAY)
Z_MODE0: U3.3 (QD), U15.24 (MODE0)
Z_MODE1: U3.2 (QC), U15.25 (MODE1)
Z_MODE2: U3.1 (QB), U15.26 (MODE2)
Z_NENABLE: U3.4 (QE), U15.21 (ENBL)
Z_NRESET: U3.7 (QH), U15.16 (RESET)
Z_NSLEEP: U3.6 (QG), U15.17 (SLEEP)

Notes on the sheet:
Fan drivers
PWM extension
Power in
5V step down converter
12V step down converter
MOSFET Ext 1
MOSFET HBP
MOSFET Ext 2
End stops 2
Thermistors
End stops 1
Dallas Temp
EEPROM
DAC

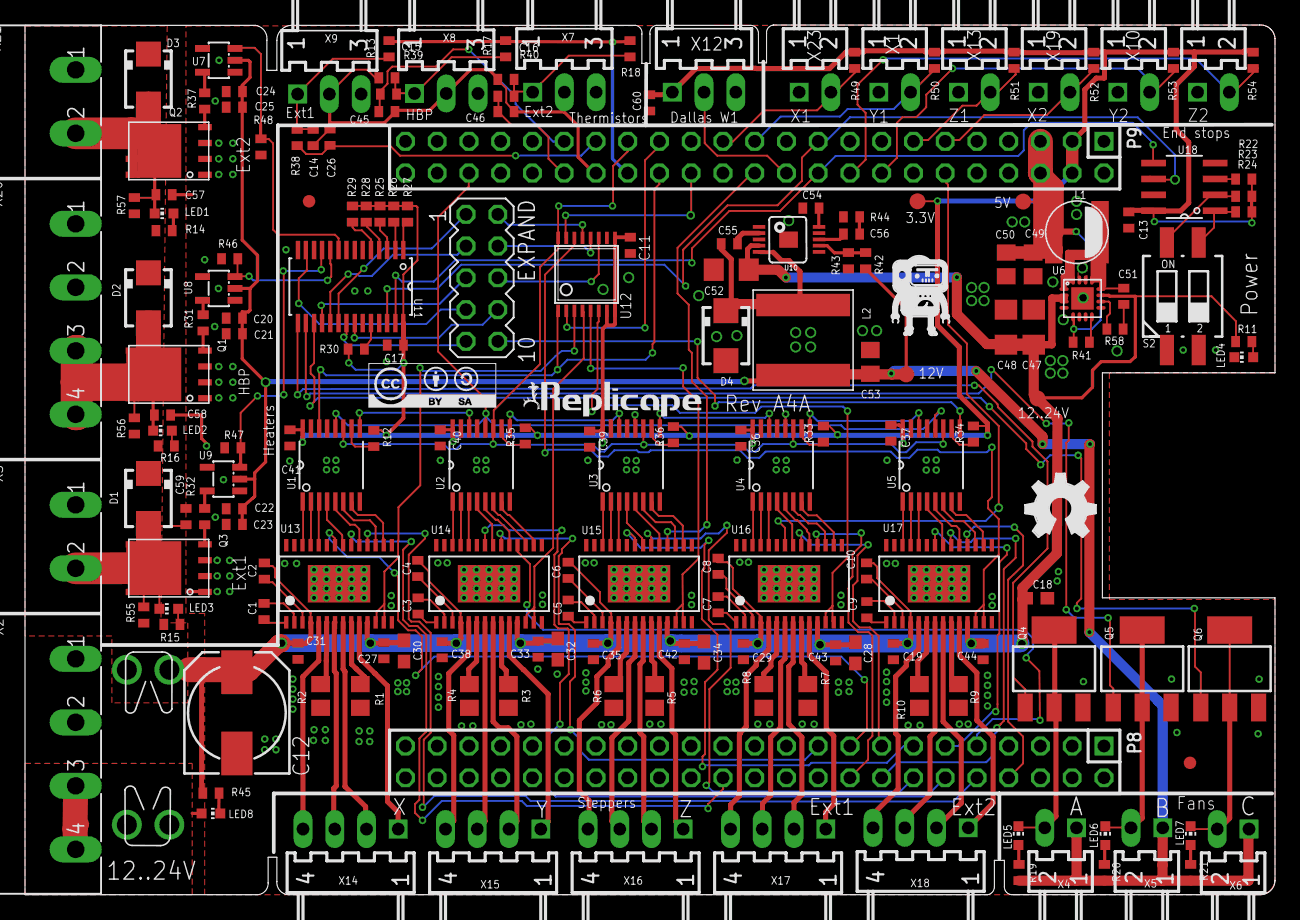
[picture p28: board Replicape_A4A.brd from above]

Board: 2 copper layers, 100.0 x 69.6 mm, 193 parts (0 on the bottom side), 192 nets.

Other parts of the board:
U$1: LOGO_BIG

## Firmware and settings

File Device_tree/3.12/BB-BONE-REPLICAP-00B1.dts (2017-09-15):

/*
 * Copyright (C) 2013 Intelligent Agent AS	<elias@iagent.no>
 *
 * This program is free software; you can redistribute it and/or modify
 * it under the terms of the GNU General Public License version 2 as
 * published by the Free Software Foundation.
 */



/dts-v1/;
/plugin/;

/ {
    compatible = "ti,beaglebone", "ti,beaglebone-black";

    /* identification */
    part-number = "BB-BONE-REPLICAP";
    version = "00B1";

    /* state the resources this cape uses */
    exclusive-use =
        /* the pin header P8 uses */
        "P8.8",  /* FAULT_EXT_2	*/
        "P8.9",  /* FAULT_Y 	*/
        "P8.10", /* FAULT_X 	*/
        "P8.11", /* STEP_H	*/
        "P8.12", /* STEP_Y      */
        "P8.13", /* STEP_Z      */
        "P8.14", /* DIR_Z       */
        "P8.15", /* DIR_E 	*/
        "P8.16", /* DIR_H 	*/
        "P8.17", /* STEP_X      */
        "P8.18", /* FAULT_E	*/
        "P8.19", /* DIR_Y       */
        "P8.26", /* DIR_X       */
        /* the pin header P9 uses */
        "P9.11", /* END_STOP_X2	*/
        "P9.12", /* STEP_E 	*/
        "P9.13", /* END_STOP_Z1	*/
        "P9.16", /* SERVO_0     */
        "P9.18", /* SERVO_1	*/
        "P9.22", /* Dallas 1W   */
        "P9.23", /* END_STOP_Y1 */
        "P9.24", /* FAULT_Z     */
        "P9.25", /* END_STOP_X1	*/
        "P9.28", /* END_STOP_Y2	*/
        "P9.30", /* SPI1_MOSI	*/
        "P9.31", /* SPI1_SCLK	*/
        "P9.33", /* AIN4        */
        "P9.35", /* AIN6        */
        "P9.36", /* AIN5        */
	"P9.41", /* ENABLE_PWM  */
        "P9.42"; /* SPI1_CS1	*/

    fragment@0 {
        target = <&am33xx_pinmux>;
        __overlay__ {
            bone_replicape_spi1_pins: pinmux_replicape_spi1_pins {
                pinctrl-single,pins = <
                    0x190 0x13	/* P9_31 = mcasp0_aclkx.spi1_sclk				 , OUTPUT_PULLUP | MODE3 */
                    0x194 0x33	/* P9_29 = mcasp0_fsx.spi1_d0					 , INPUT_PULLUP  | MODE3 */
                    0x198 0x13	/* P9_30 = mcasp0_axr0.spi1_d1					 , OUTPUT_PULLUP | MODE3 */
                    0x164 0x12  /* P9_42 = GPIO0_7 =  eCAP0_in_PWM0_out.gpio0[7]                 , OUTPUT_PULLUP | MODE2 */
                >;
            };					
            pruicss_stepper_pins: pinmux_pruicss_stepper_pins{
                pinctrl-single,pins = <
                    0x038 0x07 // P8_16 (3)  = DIR_H     	= GPIO1_14
                    0x03C 0x07 // P8_15 (4)  = DIR_E    	= GPIO1_15
                    0x028 0x07 // P8_14 (5)  = DIR_Z   	 	= GPIO0_26
                    0x02C 0x07 // P8_17 (6)  = STEP_X 	 	= GPIO0_27
                    0x034 0x07 // P8_11 (22) = step_H    	= GPIO1_13	
                    0x030 0x07 // P8_12 (23) = Step_y	 	= GPIO1_12
                    0x024 0x07 // P8_13 (24) = Step_z	 	= GPIO0_23
                    0x020 0x07 // P8_19 (25) = Dir_y 	 	= GPIO0_22
                    0x07C 0x07 // P8_26      = Dir_x		= GPIO1_29
                    0x078 0x07 // P9_12      = step E    	= GPIO1_28
                >;
            };		

            stepper_fault_pins: pinmux_stepper_fault_pins{
                pinctrl-single,pins = <
                    0x094 0x37 // P8_8  = FAULT H = GPIO2_3
                    0x09C 0x37 // P8_9  = FAYLT Y = GPIO2_5
                    0x098 0x37 // P8_10 = FAULT X = GPIO2_4
                    0x08C 0x37 // P8_18 = FAULT E = GPIO2_1
                    0x184 0x37 // P9_24 = FAULT Z = GPIO0_15
                >;
            };

            end_stop_pins: pinmux_end_stop_pins{
                pinctrl-single,pins = <
                    0x1AC 0x37 // P9_25 = End stop X1  = GPIO3_21
                    0x070 0x37 // P9_11 = End stop X2  = GPIO0_30
                    0x044 0x37 // P9_23 = End stop Y1  = GPIO1_17
                    0x074 0x37 // P9_13 = End stop Z1  = GPIO0_31
                    0x158 0x37 // P9_18 = End stop Z2  = GPIO0_4
		    0x19C 0x37 // P9_28 = End stop Y2  = GPIO3_17
                >;
            };
            dallas_w1_pins: pinmux_dallas_w1_pins {
                pinctrl-single,pins = <
		            0x150 0x37	// Dallas 1W
                >;
            };

            pwm_enable_pins: pinmux_pwm_enable_pins{
                pinctrl-single,pins = <
			            0x1B0 0x17 
                >;
            };

	    clkout2_pin: pinmux_clkout2_pin {
                pinctrl-single,pins = < 
                        0x1b4 (PIN_OUTPUT_PULLDOWN | MUX_MODE7) /* xdma_event_intr1.clkout2 */
                >;
            };

            servo_pins: pinmux_servo_pins {
                pinctrl-single,pins = <
                        BONE_P9_14 (PIN_OUTPUT_PULLDOWN | MUX_MODE6)      // Servo 0 = GPIO1_18
                        BONE_P9_16 (PIN_OUTPUT_PULLDOWN | MUX_MODE6)      // Servo 1 = GPIO1_19
                >;
            };
        };
    };

    fragment@1 {
        target = <&spi1>;
        __overlay__ {
            #address-cells 	= <1>;
            #size-cells 	= <0>;
            status		= "okay";
            pinctrl-names	= "default";
            pinctrl-0		= <&bone_replicape_spi1_pins>;	
            cs-gpios 		= <&gpio0 7 0>;

            stepper_control{
                #address-cells 	  = <1>;
                #size-cells 	  = <0>;
                compatible 	  = "spidev";
                reg 		  = <1>;
                spi-max-frequency = <16000000>;
            };
        };
    };

    fragment@2{
        target = <&pruss>;
        __overlay__{
            status = "okay";
            pinctrl-names = "default";
            pinctrl-0 	  = <&pruicss_stepper_pins>;

            stepper_x{
                pin-names 	= "Replic:pru-step_x", "Replic:pru-dir_x";		
                gpios 		= <&gpio0 27 0
		                 	   &gpio1 29 0>; 
            };			
            stepper_y{
                pin-names 	= "Replic:pru-step_y", "Replic:pru-dir_y";		
                gpios 		=<&gpio1 12 0
		                 	  &gpio0 22 0>; 
            };
            stepper_z{
                pin-names 	= "Replic:pru-step_z", "Replic:pru-dir_z";		
                gpios 		= <&gpio0 23 0
		                 	   &gpio0 26 0>; 
            };
            stepper_ext_1{
                pin-names 	= "Replic:pru-step_ext_1", "Replic:pru-dir_ext_1";		
                gpios 		= <&gpio1 28 0
		                 	   &gpio1 15 0>; 
            };
            stepper_ext_2{
                pin-names 	= "Replic:pru-step_ext_2", "Replic:pru-dir_ext_2";		
                gpios 		= <&gpio1 13 0
		                 	   &gpio1 14 0>; 
            };
        };
    };

    fragment@3 {
        target = <&baseboard_beaglebone_black>;
        __overlay__ {			
            #address-cells = <1>;
            #size-cells = <1>;							

            gpio_keys {
                compatible = "gpio-keys";
                pinctrl-names = "default";
                pinctrl-0 = <&end_stop_pins>;
                pinctrl-1 = <&stepper_fault_pins>;
                #address-cells = <1>;
                #size-cells = <0>;
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

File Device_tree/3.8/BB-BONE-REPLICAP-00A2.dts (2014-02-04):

/*
 * Copyright (C) 2013 Intelligent Agent AS	<elias@iagent.no>
 *
 * This program is free software; you can redistribute it and/or modify
 * it under the terms of the GNU General Public License version 2 as
 * published by the Free Software Foundation.
 */
/dts-v1/;
/plugin/;

/ {
	compatible = "ti,beaglebone", "ti,beaglebone-black";

	/* identification */
	part-number = "BB-BONE-REPLICAP";
	version = "00A2";

	/* state the resources this cape uses */
	exclusive-use =
		/* the pin header P8 uses */
		"P8.16", /* (3) DIR_EXT_2 	*/
		"P8.15", /* (4) DIR_EXT_1 	*/
		"P8.14", /* (5) DIR_Z 		*/
		"P8.17", /* (6) STEP_X 		*/
		"P8.7",  /* END_STOP_Y1 */
		"P8.8",  /* FAULT_EXT_2	*/
		"P8.9",  /* FAULT_Y 	*/
		"P8.10", /* FAULT_x 	*/
		"P8.18", /* FAULT_EXT_1	*/
		"P8.11", /* (22) STEP_EXT_2	*/
		"P8.12", /* (23) STEP_Y		*/
		"P8.13", /* (24) STEP_Z		*/
		"P8.19", /* (25) DIR_Y		*/
		"P8.26", /* DIR_X		*/
		/* the pin header P9 uses */
		"P9.11", /* END_STOP_Z1	*/
		"P9.12", /* STEP_EXT_1	*/
		"P9.13", /* END_STOP_X2	*/
		"P9.18", /* END_STOP_Z2	*/
		"P9.24", /* FAULT_Z		*/
		"P9.25", /* END_STOP_Y2	*/
		"P9.26", /* END_STOP_X1	*/
		"P9.28", /* SPI1_CS0 	*/
		"P9.29", /* SPI1_MISO   */
		"P9.30", /* SPI1_MOSI	*/
		"P9.31", /* SPI1_SCLK	*/
		"P9.33", /* AIN4		*/
		"P9.35", /* AIN6		*/
		"P9.36", /* AIN5		*/
		"P9.42", /* SPI1_CS1	*/
		/* Hardware IP cores in use */
		"spi1", 
		"pruss"; 

	fragment@0 {
		target = <&am33xx_pinmux>;
		__overlay__ {
			bone_replicape_spi1_pins: pinmux_replicape_spi1_pins {
				pinctrl-single,pins = <
					0x190 0x13	/* P9_31 = mcasp0_aclkx.spi1_sclk				 , OUTPUT_PULLUP | MODE3 */
					0x194 0x33	/* P9_29 = mcasp0_fsx.spi1_d0					 , INPUT_PULLUP  | MODE3 */
					0x198 0x13	/* P9_30 = mcasp0_axr0.spi1_d1					 , OUTPUT_PULLUP | MODE3 */
					0x19c 0x13	/* P9_28 = mcasp0_ahclkr.spi1_cs0				 , OUTPUT_PULLUP | MODE3 */					
					0x164 0x12  /* P9_42 = GPIO0_7 =  eCAP0_in_PWM0_out.gpio0[7] , OUTPUT_PULLUP | MODE2 */
				>;
			};					
			pruicss_stepper_pins: pinmux_pruicss_stepper_pins{
				pinctrl-single,pins = <
					0x038 0x07 // P8_16 (3)  = DIR_EXT_2	= GPIO1_14
					0x03C 0x07 // P8_15 (4)  = DIR_EXT_1	= GPIO1_15
					0x028 0x07 // P8_14 (5)  = DIR_Z   	 	= GPIO0_26
					0x02C 0x07 // P8_17 (6)  = STEP_X 	 	= GPIO0_27
				 	0x034 0x07 // P8_11 (22) = step_ext_2 	= GPIO1_13	
					0x030 0x07 // P8_12 (23) = Step_y	 	= GPIO1_12
					0x024 0x07 // P8_13 (24) = Step_z	 	= GPIO0_23
					0x020 0x07 // P8_19 (25) = Dir_y 	 	= GPIO0_22
					0x07C 0x07 // P8_26 	 = Dir_x		= GPIO1_29
					0x078 0x07 // P9_12 	 = step ext 1 	= GPIO1_28
				>;
			};		
		
			stepper_fault_pins: pinmux_stepper_fault_pins{
				pinctrl-single,pins = <
					0x094 0x37 // P8_8  = Fault Ext 2 	= GPIO2_2    gpmc_oen_ren.gpio2[3]  
					0x09C 0x37 // P8_9  = FAYLT Y		= GPIO2_5
					0x098 0x37 // P8_10 = FAULT X     	= GPIO2_4    gpmc_wen.gpio2[4]      
					0x08C 0x37 // P8_18 = Fault_ext 1	= GPIO2_1
					0x184 0x37 // P9_24 = Fault Z		= GPIO0_15
				>;
			};

			end_stop_pins: pinmux_end_stop_pins{
				pinctrl-single,pins = <
					0x090 0x37 // P8_7  = End stop X1  = GPIO2_2
					0x070 0x37 // P9_11 = End stop Y1  = GPIO0_30
					0x074 0x37 // P9_13 = End stop Z1  = GPIO0_31
					0x158 0x37 // P9_18 = End stop Z2  = GPIO0_4
					0x1AC 0x37 // P9_25 = End stop Y2  = GPIO3_21
					0x180 0x37 // P9_26 = End stop X2  = GPIO0_14
				>;
			};
		};
	};

	fragment@1 {
		target = <&spi1>;
		__overlay__ {
			#address-cells 	= <1>;
			#size-cells 	= <0>;
			status			= "okay";
			pinctrl-names	= "default";
			pinctrl-0		= <&bone_replicape_spi1_pins>;	
			cs-gpios 		= <&gpio4 17 0>, <&gpio1 7 0>;

			stepper_control{
				#address-cells 	  = <1>;
				#size-cells 	  = <0>;
				compatible 		  = "spidev";
				reg 			  = <0>;
				spi-max-frequency = <16000000>;
			};

			stepper_current{
				#address-cells 	  = <1>;
				#size-cells 	  = <0>;
				compatible 		  = "spidev";
				reg 			  = <1>;
				spi-max-frequency = <16000000>;
			};
		};
	};

	fragment@2{
		target = <&pruss>;
		__overlay__{
			status = "okay";
			pinctrl-names = "default";
			pinctrl-0 	  = <&pruicss_stepper_pins>;

			stepper_x{
				pin-names 	= "Replic:pru-step_x", "Replic:pru-dir_x";		
				gpios 		= <&gpio1 27 0
						 	   &gpio2 29 0>; 
			};			
			stepper_y{
				pin-names 	= "Replic:pru-step_y", "Replic:pru-dir_y";		
				gpios 		=<&gpio2 12 0
						 	  &gpio1 22 0>; 
			};
			stepper_z{
				pin-names 	= "Replic:pru-step_z", "Replic:pru-dir_z";		
				gpios 		= <&gpio1 23 0
						 	   &gpio1 26 0>; 
			};
			stepper_ext_1{
				pin-names 	= "Replic:pru-step_ext_1", "Replic:pru-dir_ext_1";		
				gpios 		= <&gpio2 28 0
						 	   &gpio2 15 0>; 
			};
			stepper_ext_2{
				pin-names 	= "Replic:pru-step_ext_2", "Replic:pru-dir_ext_2";		
				gpios 		= <&gpio2 13 0
						 	   &gpio2 14 0>; 
			};
		};
	};

	fragment@3 {
		target = <&ocp>;
		__overlay__ {			
			#address-cells = <1>;
			#size-cells = <1>;							

			tscadc {
				compatible = "ti,ti-tscadc";
				reg = <0x44e0d000 0x1000>;

				interrupt-parent = <&intc>;	
				interrupts = <16>;
				ti,hwmods = "adc_tsc";
				status = "okay";

				tsc {
					ti,wires = <4>;
				};
				adc {
					ti,adc-channels = <4>;
				};
			};

			thermistors{
				compatible = "bone-iio-helper";
				vsense-name  = "AIN4", "AIN5", "AIN6", "AIN7";
				vsense-scale = <100     100     100     100 >;
				status = "okay";
			};
			gpio_keys {
				compatible = "gpio-keys";
				pinctrl-names = "default";
				pinctrl-0 = <&end_stop_pins>;
				#address-cells = <1>;
				#size-cells = <0>;
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

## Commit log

2013-11-18 Redid the readme, added a license file, deleted the software
    [HipsterBot.cfg, Makerbot_cupcake.cfg, Thing.cfg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]
2014-01-12 Added a new Device tree overlay file for Kernel 3.12
2014-01-27 Added the inital revision of Reach (rev A0). The GERBER shoudl be ok, likewise the pin diagram and the BOM, but the pin-mux and wire diagrams are not updated.
    [Reach_A0.GBL, Reach_A0.GBO, Reach_A0.GBP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]
2014-02-04 Changed device tree files to kernel 3.12 and cleaned up a bit
2014-05-09 Added a test script and a service to test Replicape
    [Replicape_BOM_rev_A4A.xls]
2014-05-13 Added a Readh overlay and eeprom
    [Reach_Rev_A0_pin-mux.ods]
2014-05-13 changed case on folder in systemd script
2014-08-26 Still working on the requirements
    [Replicape_A5.brd, Replicape_A5.sch, Replicape_BOM_rev_A5.xls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]
2014-09-03 Added first version of Reason hall effect end stop sensor
    [Reason.GBL, Reason.GBO, Reason.GBP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]
2014-09-20 New Reason, bigger holes.
    [Reason.GBL, Reason.GBO, Reason.GBP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]
2015-05-03 Added first version of Replicape Rev B1
    [Replicape_B1.brd, Replicape_B1.sch, Replicape_Rev_B1_pin-mux.ods]
2015-05-03 Fixed thermals
    [Replicape_B1.brd]
2015-05-06 Added eagleup
    [Replicape_B1.brd, Replicape_B1.sch]
2015-05-07 Added the last components to the PCB and made a pretty picture of it
2015-08-19 Added EEPROM for developer edition
    [Replicape_B1.brd, Replicape_B1.sch, Replicape_Rev_B1_pin-mux.ods]
2015-09-09 Added Rev B2
    [Replicape.fzz, Replicape_B2.brd, Replicape_B2.sch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]
2015-10-02 Added skp for A4A
    [Untitled.skp]
2015-10-09 Added the centroid, ready for sedning in files.
    [BOM_replicape_b3.xls, Replicape_B3.brd, Replicape_B3.sch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]
2015-10-28 Started on REach for rev B
    [Reach_B0.brd, Reach_B0.sch, Reach_BOM_rev_B0.xls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]
2015-12-08 Updated readmen
    [Reach_B0.brd, Reach_Rev_B0_pin-mux.ods, Replicape_B1.brd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]
2015-12-23 Disable steppers after testing
2016-07-06 Added new version eeprom data
    [BOM_replicape_b3.xls, Reach_B0.brd, Reach_B0.sch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]
2017-01-23 Added a Collada (DAE) file
    [Reach_B0.brd, Reach_B0.sch]
2017-01-31 Added .stl
2017-02-17 Added latest revison
    [BOM.csv, BOM.xlsx, Pin-mux.ods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]
2017-09-15 Committing Rev B4, and cleaning up old stuff before moving repo
    [Amsung.xls, BOM.csv, BOM.xlsx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]

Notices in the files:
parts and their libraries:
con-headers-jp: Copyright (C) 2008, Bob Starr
